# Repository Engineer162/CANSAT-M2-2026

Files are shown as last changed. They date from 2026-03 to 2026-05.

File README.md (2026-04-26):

# CANSAT-M2-2026 "Rod From God MK1"

This repository contains all the sources for a highly advanced CANSAT based on an STM32 MCU and featuring a rechargeable lithium polymer battery.

Core hardware fields:

| Component | Model | Manufacturer |
| --- | --- | --- |
| STM32 MCU (core) | STM32H7S3L8H6 | STMicroelectronics |

Power system:

| Component | Model | Manufacturer |
| --- | --- | --- |
| STM32 MCU (power)  | STM32L031G6U6 | STMicroelectronics |
| USB-C Connector | 12402012E212A | Amphenol |
| Battery Management | BQ25895RTWT | Texas Instruments  |
| PD Negotiation | TPS25730DREFR | Texas Instruments  |
| Battery | 1260110 (10000mAh LiPo) | TBD |

Additionally, it features numerous different sensors for logging, as listed below:

| Sensor | Model | Manufacturer |
| --- | --- | --- |
| IMU | ICM-42688-PC | Tokmas |
| Barometer | BMP581 | BOSCH |
| Magnetometer | MMC5983MA | MEMSIC |
| Temperature (outside) | TMP121AIDBVR | Texas Instruments  |
| Temperature (inside)  | TMP121AIDBVR | Texas Instruments  |
| Ground distance (ToF) | VL53L1CXV0FY/1 | STMicroelectronics |

And debugging/programming is done via a TAG-CONNECT TC2050-IDC "Plug-Of-Nails™" connector.

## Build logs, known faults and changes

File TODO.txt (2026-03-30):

TODO:

Check sensor INT pins to see if they are active_low or active_high.
Check sensor CS pins to see if they are active_low or active_high.
Check if the above pins need to be assigned as pin context to Application or otherwise.

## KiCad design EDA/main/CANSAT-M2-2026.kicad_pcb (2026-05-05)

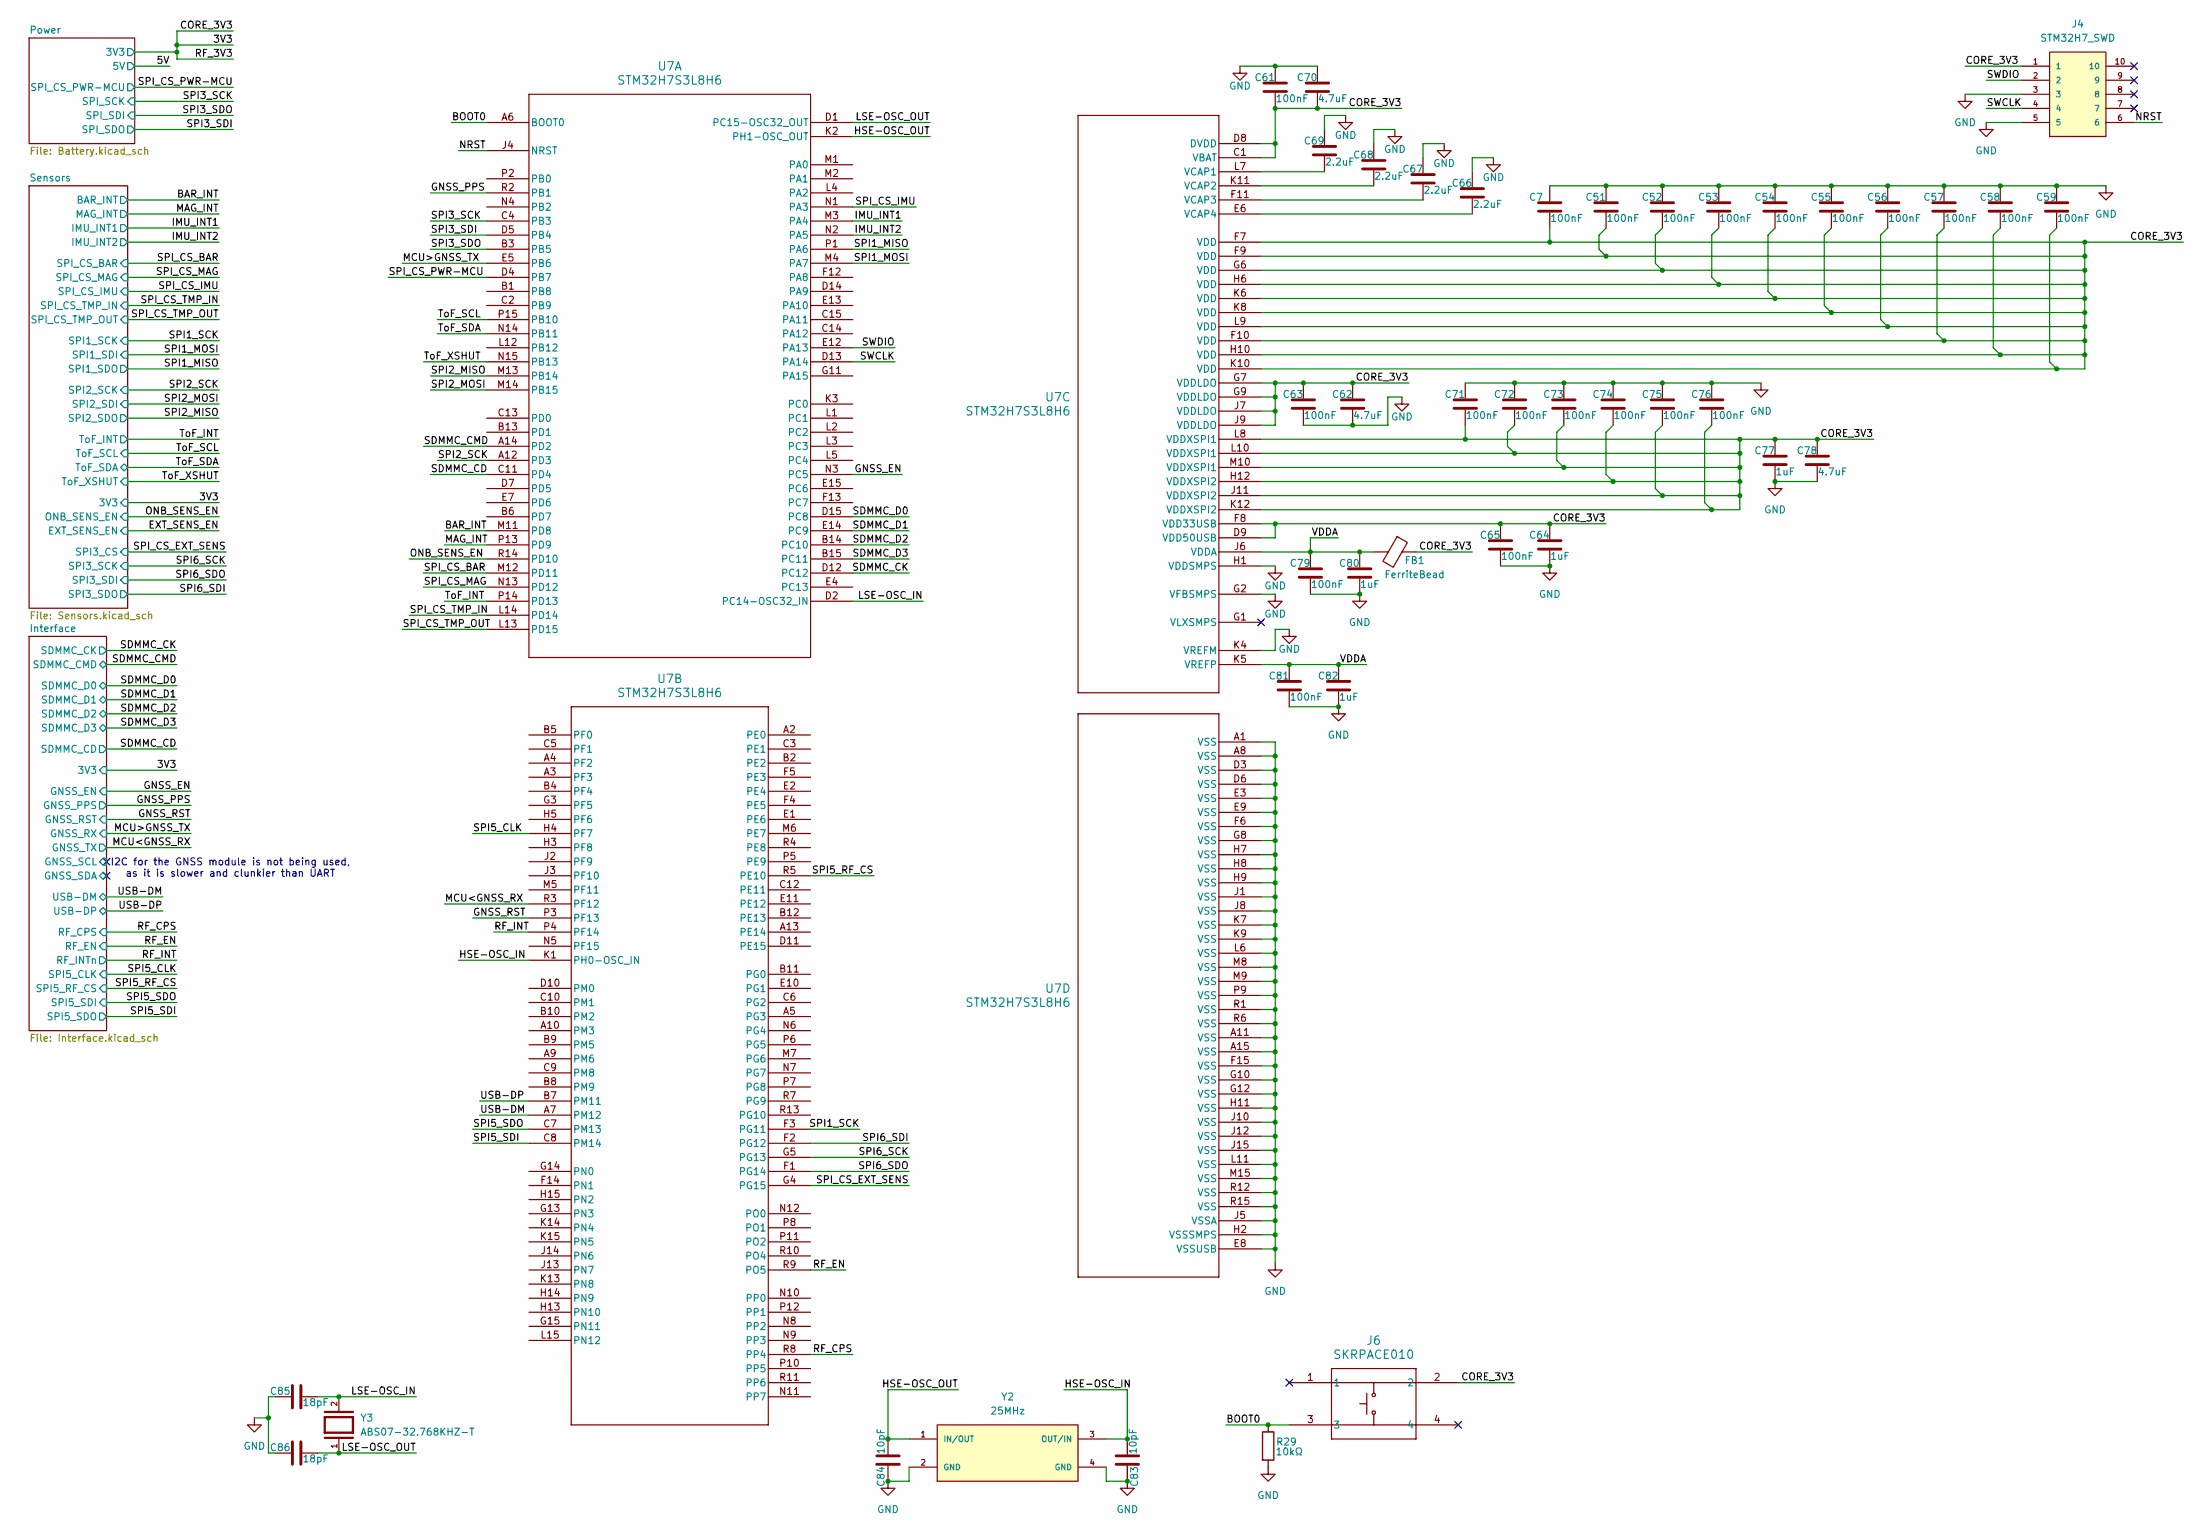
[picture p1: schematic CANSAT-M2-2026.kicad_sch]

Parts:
C7, C51, C52, C53, C54, C55, C56, C57, C58, C59, C61, C63, C65, C71, C72, C73, C74, C75, C76, C79, C81: 100nF; C_0402_1005Metric; Manufacturer Part CL05B104KP5NNNC
C62, C70, C78: 4.7uF; C_0603_1608Metric; Manufacturer Part CL10A475KP8NNNC
C64, C77, C80, C82: 1uF; C_0603_1608Metric; Manufacturer Part CL10B105MO8NNWC
C66, C67, C68, C69: 2.2uF; C_0603_1608Metric; Manufacturer Part CL10A225KO8NNNC
C83, C84: 10pF; C_0402_1005Metric; Manufacturer Part CL05C100JB5NNNC
C85, C86: 18pF; C_0402_1005Metric; Manufacturer Part CL05C180JB5NNNC
FB1: FerriteBead; L_0603_1608Metric; Manufacturer Part MMZ1608D121CTAH0
J4: STM32H7_SWD; TAG-CONNECT_TC2050-IDC; PARTREV A; DigiKey_Part_Number TC2050-IDC-ND
J6: SKRPACE010; SW_SKRPACE010_AAL; Manufacturer Part SKRPACE010
R29: 10kΩ; R_0402_1005Metric; Manufacturer Part RC0402FR-0710KL
U7: STM32H7S3L8H6; TFBGA225_13X13_STM; Manufacturer Part STM32H7S3L8H6H
Y2: 25MHz; XTAL_ECS-160-9-37-CKM-TR; PARTREV 2017
Y3: ABS07-32.768KHZ-T; XTAL_ABS07-32.768KHZ-T; PARTREV 08.19.15; DigiKey_Part_Number 535-9542-1-ND

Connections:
/3V3: C7.2, C51.2, C52.2, C53.2, C54.2, C55.2, C56.2, C57.2, C58.2, C59.2, C61.2, C62.1, C63.1, C64.1, C65.1, C70.2, C71.2, C72.2, C73.2, C74.2, C75.2, C76.2, C77.1, C78.1, FB1.1, J4.1, J6.2, U7.C1 (VBAT), U7.D8 (DVDD), U7.D9 (VDD50USB), U7.F7 (VDD), U7.F8 (VDD33USB), U7.F9 (VDD), U7.F10 (VDD), U7.G6 (VDD), U7.G7 (VDDLDO), U7.G9 (VDDLDO), U7.H6 (VDD), U7.H10 (VDD), U7.H12 (VDDXSPI2), U7.J7 (VDDLDO), U7.J9 (VDDLDO), U7.J11 (VDDXSPI2), U7.K6 (VDD), U7.K8 (VDD), U7.K10 (VDD), U7.K12 (VDDXSPI2), U7.L8 (VDDXSPI1), U7.L9 (VDD), U7.L10 (VDDXSPI1), U7.M10 (VDDXSPI1); also elsewhere on the board
/BAR_INT: U7.M11 (PD8); also elsewhere on the board
/BOOT0: J6.3, R29.1, U7.A6 (BOOT0)
/GNSS_EN: U7.N3 (PC5); also elsewhere on the board
/GNSS_PPS: U7.R2 (PB1); also elsewhere on the board
/GNSS_RST: U7.P3 (PF13); also elsewhere on the board
/HSE-OSC_IN: C83.2, U7.K1 (PH0-OSC_IN), Y2.3 (OUT/IN)
/HSE-OSC_OUT: C84.2, U7.K2 (PH1-OSC_OUT), Y2.1 (IN/OUT)
/IMU_INT1: U7.M3 (PA4); also elsewhere on the board
/IMU_INT2: U7.N2 (PA5); also elsewhere on the board
/LSE-OSC_IN: C85.2, U7.D2 (PC14-OSC32_IN), Y3.2
/LSE-OSC_OUT: C86.2, U7.D1 (PC15-OSC32_OUT), Y3.1
/MAG_INT: U7.P13 (PD9); also elsewhere on the board
/MCU<GNSS_RX: U7.R3 (PF12); also elsewhere on the board
/MCU>GNSS_TX: U7.E5 (PB6); also elsewhere on the board
/NRST: J4.6, U7.J4 (NRST)
/ONB_SENS_EN: U7.R14 (PD10); also elsewhere on the board
/RF_CPS: U7.R8 (PP4); also elsewhere on the board
/RF_EN: U7.R9 (PO5); also elsewhere on the board
/RF_INT: U7.P4 (PF14); also elsewhere on the board
/SDMMC_CD: U7.C11 (PD4); also elsewhere on the board
/SDMMC_CK: U7.D12 (PC12); also elsewhere on the board
/SDMMC_CMD: U7.A14 (PD2); also elsewhere on the board
/SDMMC_D0: U7.D15 (PC8); also elsewhere on the board
/SDMMC_D1: U7.E14 (PC9); also elsewhere on the board
/SDMMC_D2: U7.B14 (PC10); also elsewhere on the board
/SDMMC_D3: U7.B15 (PC11); also elsewhere on the board
/SPI1_MISO: U7.P1 (PA6); also elsewhere on the board
/SPI1_MOSI: U7.M4 (PA7); also elsewhere on the board
/SPI1_SCK: U7.F3 (PG11); also elsewhere on the board
/SPI2_MISO: U7.M13 (PB14); also elsewhere on the board
/SPI2_MOSI: U7.M14 (PB15); also elsewhere on the board
/SPI2_SCK: U7.A12 (PD3); also elsewhere on the board
/SPI3_SCK: U7.C4 (PB3); also elsewhere on the board
/SPI3_SDI: U7.D5 (PB4); also elsewhere on the board
/SPI3_SDO: U7.B3 (PB5); also elsewhere on the board
/SPI5_CLK: U7.H4 (PF7); also elsewhere on the board
/SPI5_RF_CS: U7.R5 (PE10); also elsewhere on the board
/SPI5_SDI: U7.C8 (PM14); also elsewhere on the board
/SPI5_SDO: U7.C7 (PM13); also elsewhere on the board
/SPI6_SCK: U7.G5 (PG13); also elsewhere on the board
/SPI6_SDI: U7.F2 (PG12); also elsewhere on the board
/SPI6_SDO: U7.F1 (PG14); also elsewhere on the board
/SPI_CS_BAR: U7.M12 (PD11); also elsewhere on the board
/SPI_CS_EXT_SENS: U7.G4 (PG15); also elsewhere on the board
/SPI_CS_IMU: U7.N1 (PA3); also elsewhere on the board
/SPI_CS_MAG: U7.N13 (PD12); also elsewhere on the board
/SPI_CS_PWR-MCU: U7.D4 (PB7); also elsewhere on the board
/SPI_CS_TMP_IN: U7.L14 (PD14); also elsewhere on the board
/SPI_CS_TMP_OUT: U7.L13 (PD15); also elsewhere on the board
/SWCLK: J4.4, U7.D13 (PA14)
/SWDIO: J4.2, U7.E12 (PA13)
/ToF_INT: U7.P14 (PD13); also elsewhere on the board
/ToF_SCL: U7.P15 (PB10); also elsewhere on the board
/ToF_SDA: U7.N14 (PB11); also elsewhere on the board
/ToF_XSHUT: U7.N15 (PB13); also elsewhere on the board
/USB-DM: U7.A7 (PM12); also elsewhere on the board
/USB-DP: U7.B7 (PM11); also elsewhere on the board
/VDDA: C79.1, C80.1, C81.1, C82.1, FB1.2, U7.J6 (VDDA), U7.K5 (VREFP)
GND: C7.1, C51.1, C52.1, C53.1, C54.1, C55.1, C56.1, C57.1, C58.1, C59.1, C61.1, C62.2, C63.2, C64.2, C65.2, C66.1, C67.1, C68.1, C69.1, C70.1, C71.1, C72.1, C73.1, C74.1, C75.1, C76.1, C77.2, C78.2, C79.2, C80.2, C81.2, C82.2, C83.1, C84.1, C85.1, C86.1, J4.3, J4.5, R29.2, U7.A1 (VSS), U7.A8 (VSS), U7.A11 (VSS), U7.A15 (VSS), U7.D3 (VSS), U7.D6 (VSS), U7.E3 (VSS), U7.E8 (VSSUSB), U7.E9 (VSS), U7.F6 (VSS), U7.F15 (VSS), U7.G2 (VFBSMPS), U7.G8 (VSS), U7.G10 (VSS), U7.G12 (VSS), U7.H1 (VDDSMPS), U7.H2 (VSSSMPS), U7.H7 (VSS), U7.H8 (VSS), U7.H9 (VSS), U7.H11 (VSS), U7.J1 (VSS), U7.J5 (VSSA), U7.J8 (VSS), U7.J10 (VSS), U7.J12 (VSS), U7.J15 (VSS), U7.K4 (VREFM), U7.K7 (VSS), U7.K9 (VSS), U7.L6 (VSS), U7.L11 (VSS), U7.M8 (VSS), U7.M9 (VSS), U7.M15 (VSS), U7.P9 (VSS), U7.R1 (VSS), U7.R6 (VSS), U7.R12 (VSS), U7.R15 (VSS), Y2.2 (GND), Y2.4 (GND); also elsewhere on the board
unnamed: C69.2, U7.L7 (VCAP1)
unnamed: C68.2, U7.K11 (VCAP2)
unnamed: C67.2, U7.F11 (VCAP3)
unnamed: C66.2, U7.E6 (VCAP4)

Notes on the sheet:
I2C for the GNSS module is not being used, as it is slower and clunkier than UART

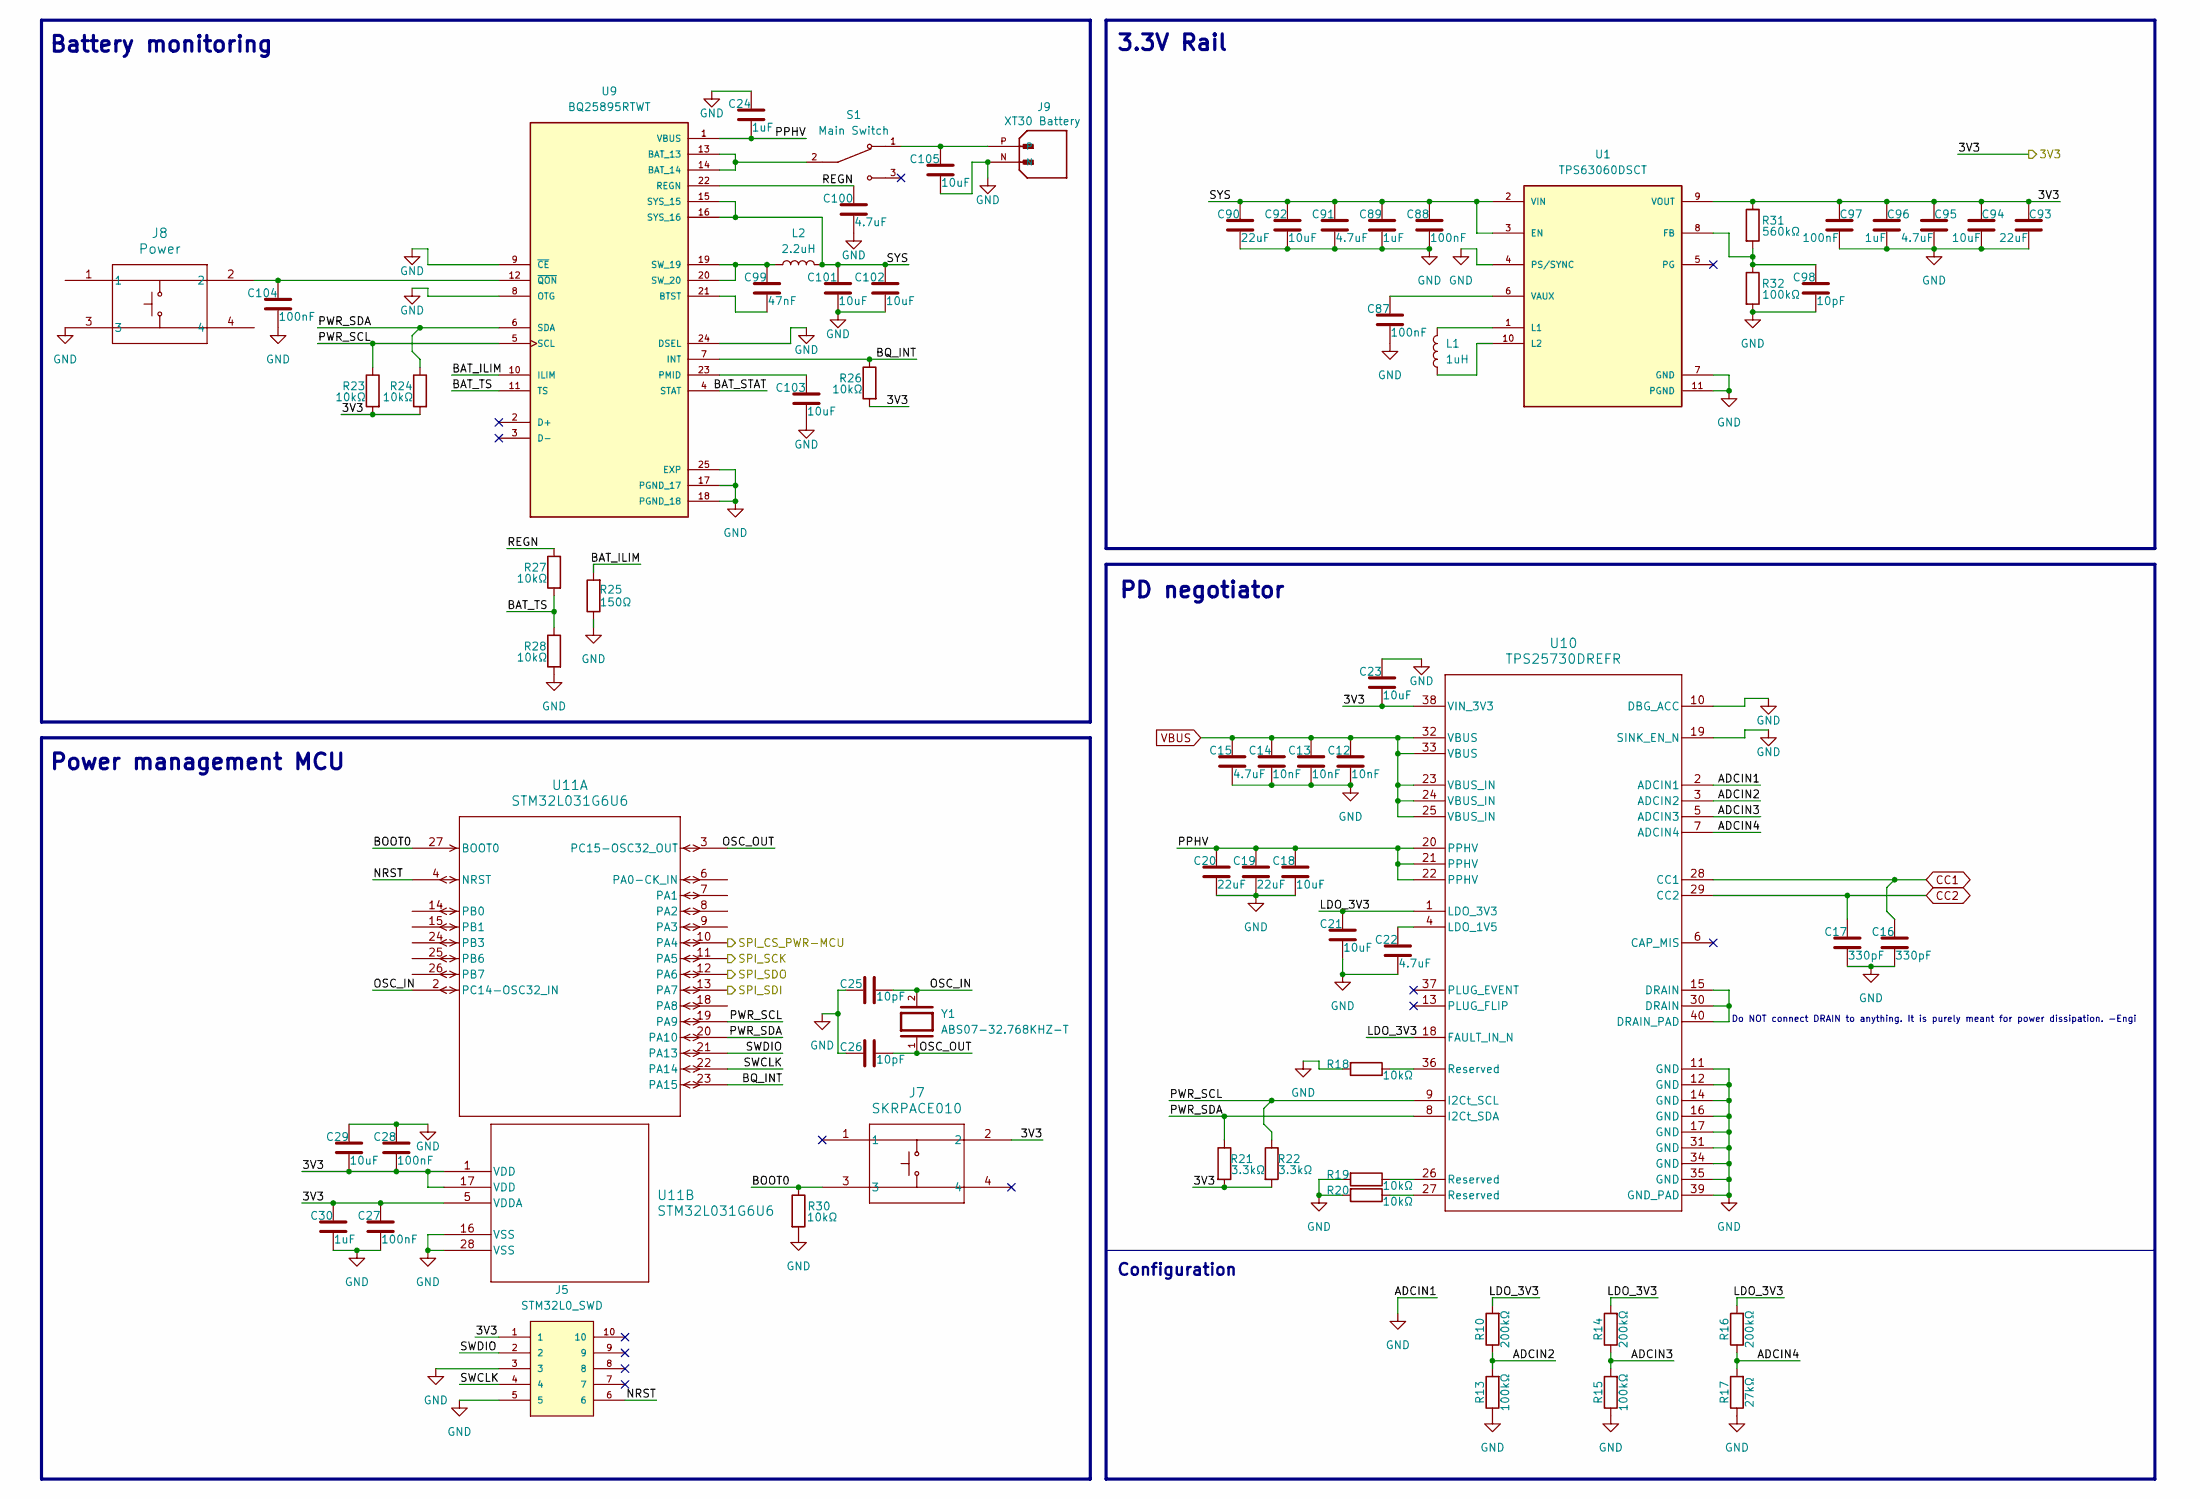
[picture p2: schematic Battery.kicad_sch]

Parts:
C12, C13, C14: 10nF; C_0402_1005Metric; Manufacturer Part CL05B103KB5NNNC
C15, C22, C91, C95, C100: 4.7uF; C_0603_1608Metric; Manufacturer Part CL10A475KP8NNNC
C16, C17: 330pF; C_0402_1005Metric; Manufacturer Part CL05C331JB5NNNC
C18, C21, C23, C29, C92, C94, C101, C102, C103, C105: 10uF; C_0603_1608Metric; Manufacturer Part CL10X106MO8NRNC
C19, C20, C90, C93: 22uF; C_0603_1608Metric; Manufacturer Part CL10A226MP8NUNE
C24, C30, C89, C96: 1uF; C_0603_1608Metric; Manufacturer Part CL10B105MO8NNWC
C25, C26, C98: 10pF; C_0402_1005Metric; Manufacturer Part CL05C100JB5NNNC
C27, C28, C87, C88, C97, C104: 100nF; C_0402_1005Metric; Manufacturer Part CL05B104KP5NNNC
C99: 47nF; C_0402_1005Metric; Manufacturer Part CL05B473KB5VPNC
J5: STM32L0_SWD; TAG-CONNECT_TC2050-IDC; PARTREV A; DigiKey_Part_Number TC2050-IDC-ND
J7: SKRPACE010; SW_SKRPACE010_AAL; Manufacturer Part SKRPACE010
J8: Power; SW_SKRPACE010_AAL; Manufacturer Part SKRPACE010
J9: XT30 Battery; AMASS_XT30PW-M; PARTREV 1.2
L1: 1uH; L_1008_2520Metric; Manufacturer Part 74438324010
L2: 2.2uH; L_Wuerth_MAPI-4020; Manufacturer Part 74438356022
R10, R14, R16: 200kΩ; R_0603_1608Metric; Manufacturer Part RC0603JR-07200KL
R13, R15: 100kΩ; R_0603_1608Metric; Manufacturer Part RC0603FR-07100KL
R17: 27kΩ; R_0603_1608Metric; Manufacturer Part RC0603FR-1027KL
R18, R19, R20, R23, R24, R26, R27, R28, R30: 10kΩ; R_0402_1005Metric; Manufacturer Part RC0402FR-0710KL
R21, R22: 3.3kΩ; R_0402_1005Metric; Manufacturer Part RC0402FR-073K3L
R25: 150Ω; R_0603_1608Metric; Manufacturer Part RC0603FR-07150RL
R31: 560kΩ; R_0402_1005Metric; Manufacturer Part RC0402FR-13560KL
R32: 100kΩ; R_0402_1005Metric; Manufacturer Part RC0402FR-07100KL
S1: Main Switch; SW_500SSP1S1M6QEA; PARTREV D
U1: TPS63060DSCT; CONV_TPS63060DSCT; PARTREV B
U9: BQ25895RTWT; QFN50P400X400X80-25N; PARTREV B
U10: TPS25730DREFR; REF0038A-MFG; Manufacturer Part TPS25730DREFR
U11: STM32L031G6U6; UFQFPN28-4x4mm; Manufacturer Part STM32L031G6U6
Y1: ABS07-32.768KHZ-T; XTAL_ABS07-32.768KHZ-T; PARTREV 08.19.15; DigiKey_Part_Number 535-9542-1-ND

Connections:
/3V3: C23.2, C27.1, C28.2, C29.2, C30.1, C93.1, C94.1, C95.1, C96.1, C97.1, J5.1, J7.2, R21.2, R22.2, R23.2, R24.2, R26.2, R31.1, U1.9 (VOUT), U10.38 (VIN_3V3), U11.1 (VDD), U11.5 (VDDA), U11.17 (VDD); also elsewhere on the board
/Power/ADCIN2: R10.1, R13.2, U10.3 (ADCIN2)
/Power/ADCIN3: R14.1, R15.2, U10.5 (ADCIN3)
/Power/ADCIN4: R16.1, R17.2, U10.7 (ADCIN4)
/Power/BAT_ILIM: R25.2, U9.10 (ILIM)
/Power/BAT_STAT: U9.4 (STAT)
/Power/BAT_TS: R27.2, R28.1, U9.11 (TS)
/Power/BOOT0: J7.3, R30.1, U11.27 (BOOT0)
/Power/BQ_INT: R26.1, U9.7 (INT), U11.23 (PA15)
/Power/LDO_3V3: C21.1, R10.2, R14.2, R16.2, U10.1 (LDO_3V3), U10.18 (FAULT_IN_N)
/Power/NRST: J5.6, U11.4 (NRST)
/Power/OSC_IN: C25.2, U11.2 (PC14-OSC32_IN), Y1.2
/Power/OSC_OUT: C26.2, U11.3 (PC15-OSC32_OUT), Y1.1
/Power/PPHV: C18.1, C19.1, C20.1, C24.2, U9.1 (VBUS), U10.20 (PPHV), U10.21 (PPHV), U10.22 (PPHV)
/Power/PWR_SCL: R22.1, R23.1, U9.5 (SCL), U10.9 (I2Ct_SCL), U11.19 (PA9)
/Power/PWR_SDA: R21.1, R24.1, U9.6 (SDA), U10.8 (I2Ct_SDA), U11.20 (PA10)
/Power/REGN: C100.1, R27.1, U9.22 (REGN)
/Power/SWCLK: J5.4, U11.22 (PA14)
/Power/SWDIO: J5.2, U11.21 (PA13)
/Power/SYS: C88.1, C89.1, C90.1, C91.1, C92.1, C101.1, C102.1, L2.2, U1.2 (VIN), U1.3 (EN), U9.15 (SYS_15), U9.16 (SYS_16)
/SPI3_SCK: U11.11 (PA5); also elsewhere on the board
/SPI3_SDI: U11.12 (PA6); also elsewhere on the board
/SPI3_SDO: U11.13 (PA7); also elsewhere on the board
/SPI_CS_PWR-MCU: U11.10 (PA4); also elsewhere on the board
CC1: C16.1, U10.28 (CC1); also elsewhere on the board
CC2: C17.1, U10.29 (CC2); also elsewhere on the board
GND: C12.2, C13.2, C14.2, C15.2, C16.2, C17.2, C18.2, C19.2, C20.2, C21.2, C22.2, C23.1, C24.1, C25.1, C26.1, C27.2, C28.1, C29.1, C30.2, C87.2, C88.2, C89.2, C90.2, C91.2, C92.2, C93.2, C94.2, C95.2, C96.2, C97.2, C98.2, C100.2, C101.2, C102.2, C103.2, C104.2, C105.2, J5.3, J5.5, J8.3, J9.N, R13.1, R15.1, R17.1, R18.2, R19.2, R20.2, R25.1, R28.2, R30.2, R32.2, U1.4 (PS/SYNC), U1.7 (GND), U1.11 (PGND), U9.8 (OTG), U9.9 (~CE), U9.17 (PGND_17), U9.18 (PGND_18), U9.24 (DSEL), U9.25 (EXP), U10.2 (ADCIN1), U10.10 (DBG_ACC), U10.11 (GND), U10.12 (GND), U10.14 (GND), U10.16 (GND), U10.17 (GND), U10.19 (SINK_EN_N), U10.31 (GND), U10.34 (GND), U10.35 (GND), U10.39 (GND_PAD), U11.16 (VSS), U11.28 (VSS); also elsewhere on the board
unnamed: C105.1, J9.P, S1.1
unnamed: R18.1, U10.36 (Reserved)
unnamed: R19.1, U10.26 (Reserved)
unnamed: R20.1, U10.27 (Reserved)
unnamed: C98.1, R31.2, R32.1, U1.8 (FB)
unnamed: L1.2, U1.1 (L1)
unnamed: L1.1, U1.10 (L2)
unnamed: C87.1, U1.6 (VAUX)
unnamed: S1.2, U9.13 (BAT_13), U9.14 (BAT_14)
unnamed: C99.2, U9.21 (BTST)
unnamed: C103.1, U9.23 (PMID)
unnamed: C99.1, L2.1, U9.19 (SW_19), U9.20 (SW_20)
unnamed: C104.1, J8.2, U9.12 (~QON)
unnamed: U10.15 (DRAIN), U10.30 (DRAIN), U10.40 (DRAIN_PAD)
unnamed: C22.1, U10.4 (LDO_1V5)
VBUS: C12.1, C13.1, C14.1, C15.1, U10.23 (VBUS_IN), U10.24 (VBUS_IN), U10.25 (VBUS_IN), U10.32 (VBUS), U10.33 (VBUS); also elsewhere on the board

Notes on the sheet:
Power management MCU
Battery monitoring
3.3V Rail
Configuration
Do NOT connect DRAIN to anything. It is purely meant for power dissipation. -Engi
PD negotiator

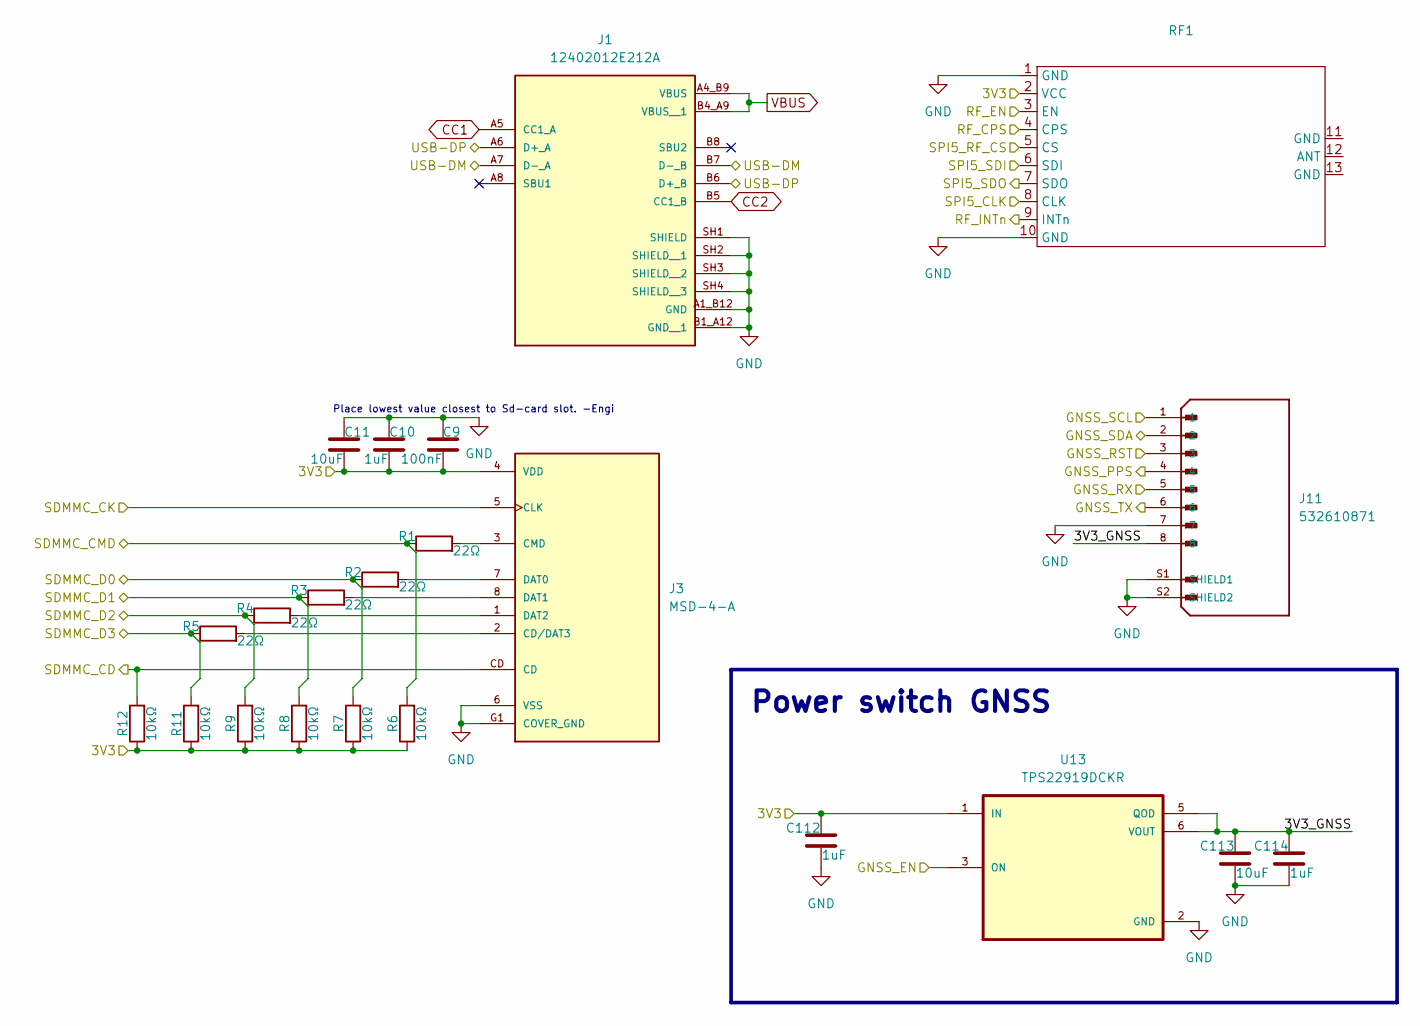
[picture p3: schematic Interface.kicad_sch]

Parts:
C9: 100nF; C_0402_1005Metric; Manufacturer Part CL05B104KP5NNNC
C10, C112, C114: 1uF; C_0603_1608Metric; Manufacturer Part CL10B105MO8NNWC
C11, C113: 10uF; C_0603_1608Metric; Manufacturer Part CL10X106MO8NRNC
J1: 12402012E212A; AMPHENOL_USB-C_12402012E212A; PARTREV 4
J3: MSD-4-A; CUI_MSD-4-A; PARTREV 1.0; DigiKey_Part_Number 2223-MSD-4-ACT-ND
J11: 532610871; MOLEX_532610871; PARTREV J
R1, R2, R3, R4, R5: 22Ω; R_0402_1005Metric; Manufacturer Part RC0402FR-0722RL
R6, R7, R8, R9, R11, R12: 10kΩ; R_0402_1005Metric; Manufacturer Part RC0402FR-0710KL
RF1: SI4463-MODULE
U13: TPS22919DCKR; SOT65P210X110-6N; Manufacturer Part TPS22919DCKR

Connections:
/3V3: C9.2, C10.2, C11.2, C112.1, J3.4 (VDD), R6.1, R7.1, R8.1, R9.1, R11.1, R12.1, RF1.2 (VCC), U13.1 (IN); also elsewhere on the board
/GNSS_EN: U13.3 (ON); also elsewhere on the board
/GNSS_PPS: J11.4; also elsewhere on the board
/GNSS_RST: J11.3; also elsewhere on the board
/Interface/3V3_GNSS: C113.1, C114.1, J11.8, U13.5 (QOD), U13.6 (VOUT)
/Interface/GNSS_SCL: J11.1
/Interface/GNSS_SDA: J11.2
/MCU<GNSS_RX: J11.6; also elsewhere on the board
/MCU>GNSS_TX: J11.5; also elsewhere on the board
/RF_CPS: RF1.4 (CPS); also elsewhere on the board
/RF_EN: RF1.3 (EN); also elsewhere on the board
/RF_INT: RF1.9 (INTn); also elsewhere on the board
/SDMMC_CD: J3.CD, R12.2; also elsewhere on the board
/SDMMC_CK: J3.5 (CLK); also elsewhere on the board
/SDMMC_CMD: R1.1, R6.2; also elsewhere on the board
/SDMMC_D0: R2.1, R7.2; also elsewhere on the board
/SDMMC_D1: R3.1, R8.2; also elsewhere on the board
/SDMMC_D2: R4.1, R9.2; also elsewhere on the board
/SDMMC_D3: R5.1, R11.2; also elsewhere on the board
/SPI5_CLK: RF1.8 (CLK); also elsewhere on the board
/SPI5_RF_CS: RF1.5 (CS); also elsewhere on the board
/SPI5_SDI: RF1.7 (SDO); also elsewhere on the board
/SPI5_SDO: RF1.6 (SDI); also elsewhere on the board
/USB-DM: J1.A7 (D-_A), J1.B7 (D-_B); also elsewhere on the board
/USB-DP: J1.A6 (D+_A), J1.B6 (D+_B); also elsewhere on the board
CC1: J1.A5 (CC1_A); also elsewhere on the board
CC2: J1.B5 (CC1_B); also elsewhere on the board
GND: C9.1, C10.1, C11.1, C112.2, C113.2, C114.2, J1.A1_B12 (GND), J1.B1_A12 (GND__1), J1.SH1 (SHIELD), J1.SH2 (SHIELD__1), J1.SH3 (SHIELD__2), J1.SH4 (SHIELD__3), J3.6 (VSS), J3.G1 (COVER_GND), J3.G2 (COVER_GND), J3.G3 (COVER_GND), J3.G4 (COVER_GND), J11.7, J11.S1 (SHIELD1), J11.S2 (SHIELD2), RF1.1 (GND), RF1.10 (GND), U13.2 (GND); also elsewhere on the board
unnamed: J3.2 (CD/DAT3), R5.2
unnamed: J3.3 (CMD), R1.2
unnamed: J3.7 (DAT0), R2.2
unnamed: J3.8 (DAT1), R3.2
unnamed: J3.1 (DAT2), R4.2
VBUS: J1.A4_B9 (VBUS), J1.B4_A9 (VBUS__1); also elsewhere on the board

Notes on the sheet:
Place lowest value closest to Sd-card slot. -Engi
Power switch GNSS

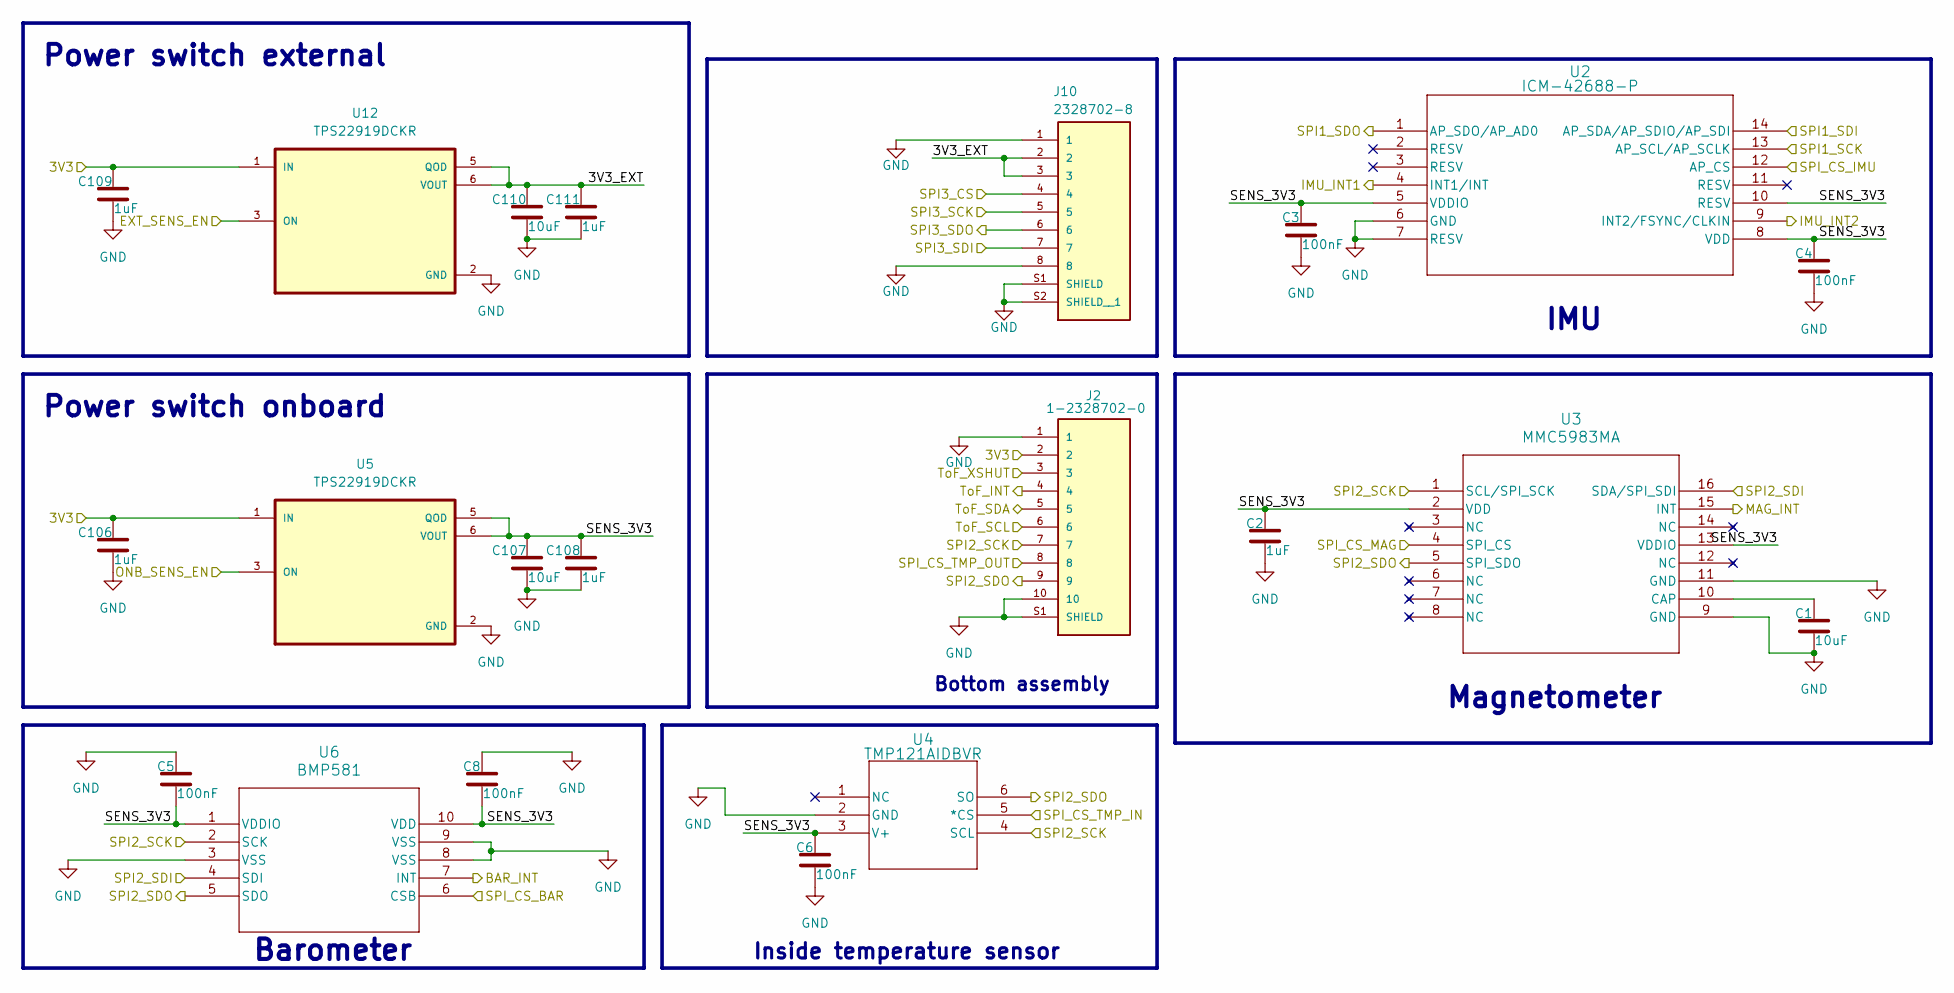
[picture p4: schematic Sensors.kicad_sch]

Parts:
C1, C107, C110: 10uF; C_0603_1608Metric; Manufacturer Part CL10X106MO8NRNC
C2, C106, C108, C109, C111: 1uF; C_0603_1608Metric; Manufacturer Part CL10B105MO8NNWC
C3, C4, C5, C6, C8: 100nF; C_0402_1005Metric; Manufacturer Part CL05B104KP5NNNC
J2: 1-2328702-0; TE_1-2328702-0; PARTREV 5; DigiKey_Part_Number A141390CT-ND
J10: 2328702-8; TE_2328702-8; PARTREV 5
U2: ICM-42688-P; LGA14_2P5X3X0P91_TDK; Manufacturer Part ICM-42688-P
U3: MMC5983MA; MMC5983MA_MEM; Manufacturer Part MMC5983MA
U4: TMP121AIDBVR; DBV6; Manufacturer Part TMP121AIDBVR
U5, U12: TPS22919DCKR; SOT65P210X110-6N; Manufacturer Part TPS22919DCKR
U6: BMP581; QFN10_BMP581_BOS; Manufacturer Part BMP581

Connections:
/3V3: C106.1, C109.1, J2.2, U5.1 (IN), U12.1 (IN); also elsewhere on the board
/BAR_INT: U6.7 (INT); also elsewhere on the board
/EXT_SENS_EN: U12.3 (ON)
/IMU_INT1: U2.4 (INT1/INT); also elsewhere on the board
/IMU_INT2: U2.9 (INT2/FSYNC/CLKIN); also elsewhere on the board
/MAG_INT: U3.15 (INT); also elsewhere on the board
/ONB_SENS_EN: U5.3 (ON); also elsewhere on the board
/SPI1_MISO: U2.1 (AP_SDO/AP_AD0); also elsewhere on the board
/SPI1_MOSI: U2.14 (AP_SDA/AP_SDIO/AP_SDI); also elsewhere on the board
/SPI1_SCK: U2.13 (AP_SCL/AP_SCLK); also elsewhere on the board
/SPI2_MISO: J2.9, U3.5 (SPI_SDO), U4.6 (SO), U6.5 (SDO); also elsewhere on the board
/SPI2_MOSI: U3.16 (SDA/SPI_SDI), U6.4 (SDI); also elsewhere on the board
/SPI2_SCK: J2.7, U3.1 (SCL/SPI_SCK), U4.4 (SCL), U6.2 (SCK); also elsewhere on the board
/SPI6_SCK: J10.5; also elsewhere on the board
/SPI6_SDI: J10.6; also elsewhere on the board
/SPI6_SDO: J10.7; also elsewhere on the board
/SPI_CS_BAR: U6.6 (CSB); also elsewhere on the board
/SPI_CS_EXT_SENS: J10.4; also elsewhere on the board
/SPI_CS_IMU: U2.12 (AP_CS); also elsewhere on the board
/SPI_CS_MAG: U3.4 (SPI_CS); also elsewhere on the board
/SPI_CS_TMP_IN: U4.5 (*CS); also elsewhere on the board
/SPI_CS_TMP_OUT: J2.8; also elsewhere on the board
/Sensors/3V3_EXT: C110.1, C111.1, J10.2, J10.3, U12.5 (QOD), U12.6 (VOUT)
/Sensors/SENS_3V3: C2.1, C3.1, C4.1, C5.2, C6.1, C8.2, C107.1, C108.1, U2.5 (VDDIO), U2.8 (VDD), U2.10 (RESV), U3.2 (VDD), U3.13 (VDDIO), U4.3 (V+), U5.5 (QOD), U5.6 (VOUT), U6.1 (VDDIO), U6.10 (VDD)
/ToF_INT: J2.4; also elsewhere on the board
/ToF_SCL: J2.6; also elsewhere on the board
/ToF_SDA: J2.5; also elsewhere on the board
/ToF_XSHUT: J2.3; also elsewhere on the board
GND: C1.2, C2.2, C3.2, C4.2, C5.1, C6.2, C8.1, C106.2, C107.2, C108.2, C109.2, C110.2, C111.2, J2.1, J2.10, J2.S1 (SHIELD), J2.S2 (SHIELD), J10.1, J10.8, J10.S1 (SHIELD), J10.S2 (SHIELD__1), U2.6 (GND), U2.7 (RESV), U3.9 (GND), U3.11 (GND), U4.2 (GND), U5.2 (GND), U6.3 (VSS), U6.8 (VSS), U6.9 (VSS), U12.2 (GND); also elsewhere on the board
unnamed: C1.1, U3.10 (CAP)

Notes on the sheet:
Power switch onboard
Barometer
Magnetometer
Bottom assembly
Inside temperature sensor
IMU
Power switch external

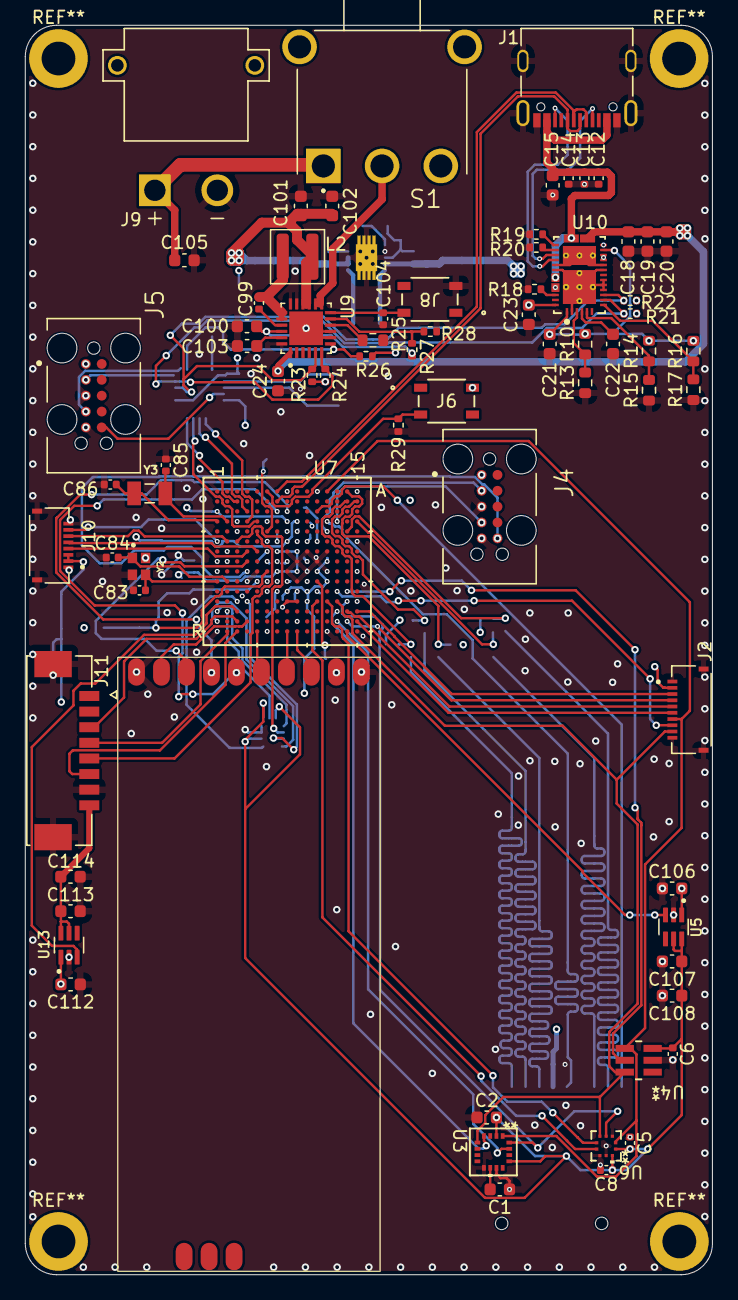
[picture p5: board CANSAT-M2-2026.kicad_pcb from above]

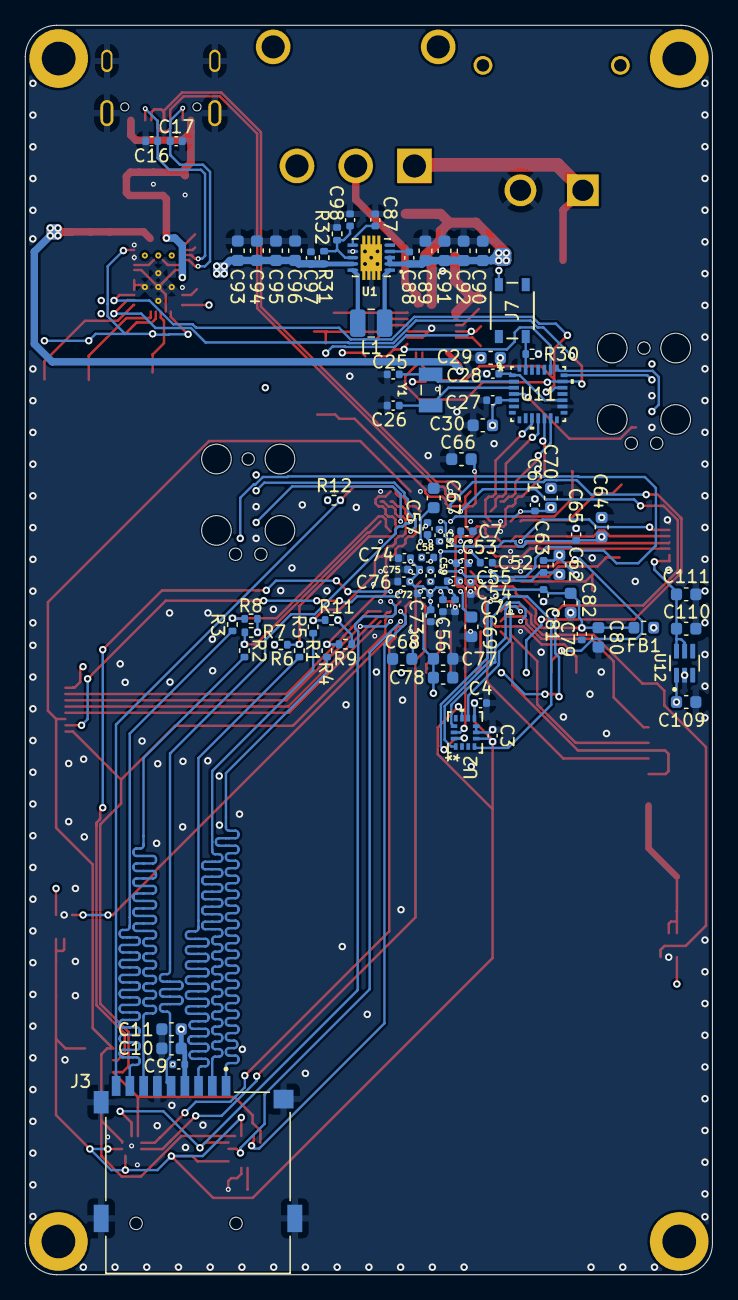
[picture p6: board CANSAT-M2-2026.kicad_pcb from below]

Board: 4 copper layers, 55.0 x 100.0 mm, 156 parts (83 on the bottom side), 109 nets.

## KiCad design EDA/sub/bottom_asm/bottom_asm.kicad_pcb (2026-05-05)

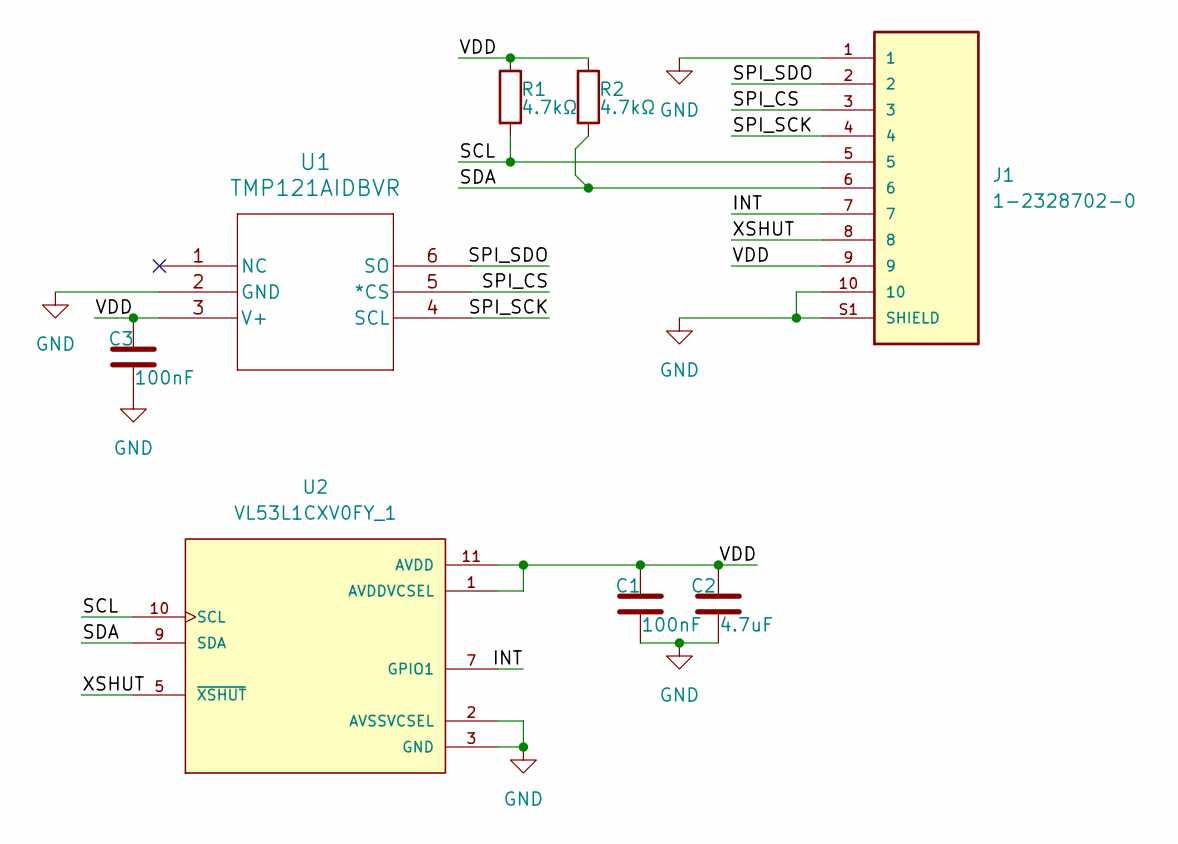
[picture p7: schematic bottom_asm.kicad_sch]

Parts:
C1, C3: 100nF; C_0402_1005Metric; Manufacturer Part CL05B104KP5NNNC
C2: 4.7uF; C_0603_1608Metric; Manufacturer Part CL10A475KP8NNNC
J1: 1-2328702-0; TE_1-2328702-0; PARTREV 5; DigiKey_Part_Number A141390CT-ND
R1, R2: 4.7kΩ; R_0402_1005Metric; Manufacturer Part RC0402JR-074K7L
U1: TMP121AIDBVR; DBV6; Manufacturer Part TMP121AIDBVR
U2: VL53L1CXV0FY_1; SENSOR_VL53L1CXV0FY_1; PARTREV 2

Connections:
/INT: J1.7, U2.7 (GPIO1)
/SCL: J1.5, R1.2, U2.10 (SCL)
/SDA: J1.6, R2.2, U2.9 (SDA)
/SPI_CS: J1.3, U1.5 (*CS)
/SPI_SCK: J1.4, U1.4 (SCL)
/SPI_SDO: J1.2, U1.6 (SO)
/VDD: C1.1, C2.1, C3.1, J1.9, R1.1, R2.1, U1.3 (V+), U2.1 (AVDDVCSEL), U2.11 (AVDD)
/XSHUT: J1.8, U2.5 (~XSHUT)
GND: C1.2, C2.2, C3.2, J1.1, J1.10, J1.S1 (SHIELD), J1.S2 (SHIELD), U1.2 (GND), U2.2 (AVSSVCSEL), U2.3 (GND), U2.4 (GND), U2.6 (GND), U2.12 (GND)

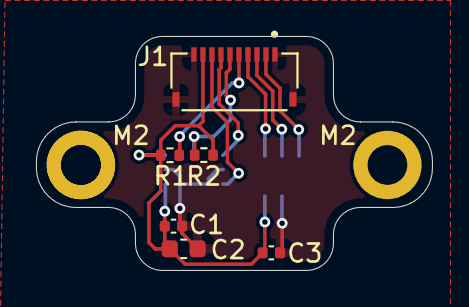
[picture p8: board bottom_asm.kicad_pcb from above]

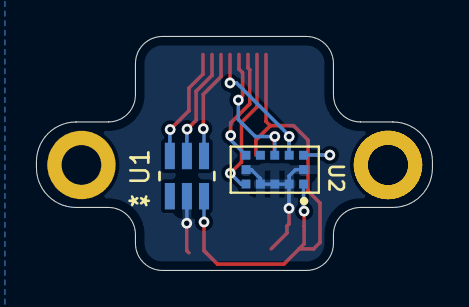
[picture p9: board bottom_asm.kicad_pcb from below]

Board: 2 copper layers, 22.0 x 13.0 mm, 10 parts (2 on the bottom side), 9 nets.

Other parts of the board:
M2, M2#2: MountingHole_2.2mm_M2_DIN965_Pad

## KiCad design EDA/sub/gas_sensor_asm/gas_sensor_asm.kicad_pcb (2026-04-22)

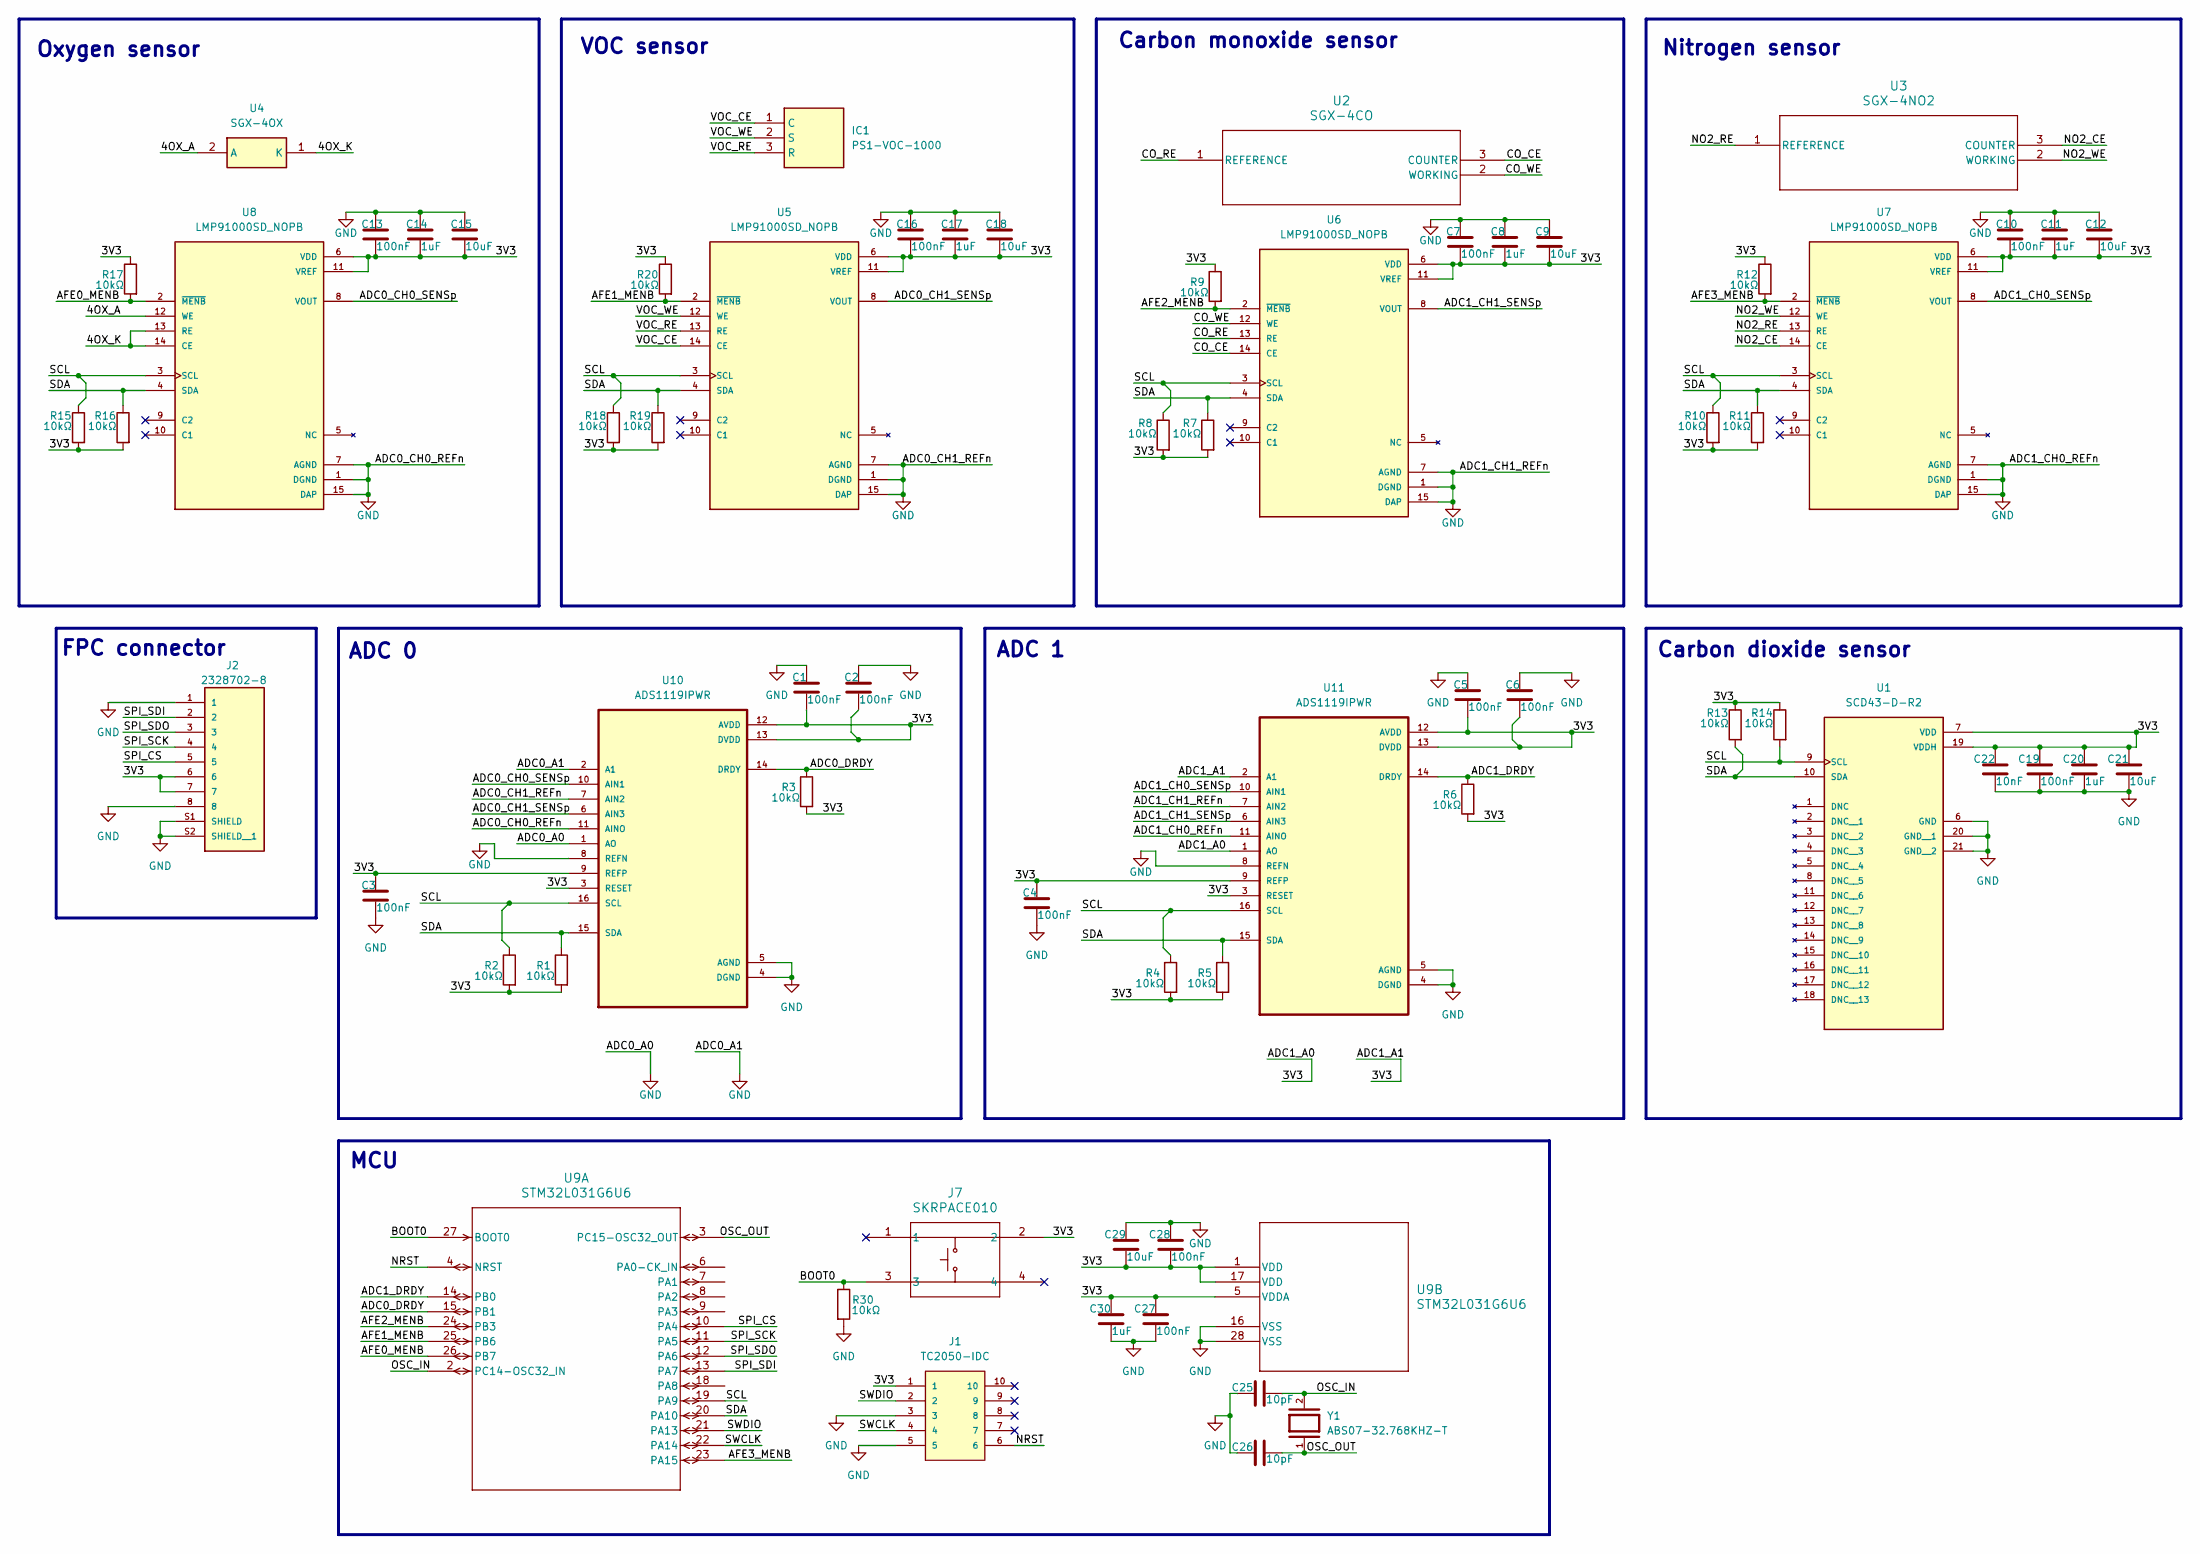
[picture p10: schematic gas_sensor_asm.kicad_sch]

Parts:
C1, C2, C3, C4, C5, C6, C7, C10, C13, C16, C19, C27, C28: 100nF; C_0402_1005Metric
C8, C11, C14, C17, C20, C30: 1uF; C_0603_1608Metric
C9, C12, C15, C18, C21, C29: 10uF; C_0603_1608Metric
C22: 10nF; C_0402_1005Metric
C25, C26: 10pF; C_0402_1005Metric
IC1: PS1-VOC-1000; PS1VOC1000; Manufacturer_Part_Number PS1-VOC-1000
J1: TC2050-IDC; TAG-CONNECT_TC2050-IDC; PARTREV A; DigiKey_Part_Number TC2050-IDC-ND
J2: 2328702-8; TE_2328702-8; PARTREV 5
J7: SKRPACE010; SW_SKRPACE010_AAL
R1, R2, R3, R4, R5, R6, R7, R8, R9, R10, R11, R12, R13, R14, R15, R16, R17, R18, R19, R20, R30: 10kΩ; R_0402_1005Metric
U1: SCD43-D-R2; XDCR_SCD43-D-R2; PARTREV 1.2
U2: SGX-4CO
U3: SGX-4NO2
U4: SGX-4OX; SGX4OX; Mouser Part Number 523-SGX-4OX
U5, U6, U7, U8: LMP91000SD_NOPB; SON50P400X400X80-15N; PARTREV I
U9: STM32L031G6U6; UFQFPN28-4x4mm
U10, U11: ADS1119IPWR; SOP65P640X120-16N
Y1: ABS07-32.768KHZ-T; XTAL_ABS07-32.768KHZ-T; PARTREV 08.19.15; DigiKey_Part_Number 535-9542-1-ND

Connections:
/3V3: C1.2, C2.2, C3.1, C4.1, C5.2, C6.2, C7.2, C8.2, C9.2, C10.2, C11.2, C12.2, C13.2, C14.2, C15.2, C16.2, C17.2, C18.2, C19.1, C20.1, C21.1, C22.1, C27.1, C28.2, C29.2, C30.1, J1.1, J2.6, J2.7, J7.2, R1.2, R2.2, R3.2, R4.2, R5.2, R6.2, R7.2, R8.2, R9.1, R10.2, R11.2, R12.1, R13.1, R14.1, R15.2, R16.2, R17.1, R18.2, R19.2, R20.1, U1.7 (VDD), U1.19 (VDDH), U5.6 (VDD), U5.11 (VREF), U6.6 (VDD), U6.11 (VREF), U7.6 (VDD), U7.11 (VREF), U8.6 (VDD), U8.11 (VREF), U9.1 (VDD), U9.5 (VDDA), U9.17 (VDD), U10.3 (RESET), U10.9 (REFP), U10.12 (AVDD), U10.13 (DVDD), U11.1 (AO), U11.2 (A1), U11.3 (RESET), U11.9 (REFP), U11.12 (AVDD), U11.13 (DVDD)
/4OX_A: U4.2 (A), U8.12 (WE)
/4OX_K: U4.1 (K), U8.13 (RE), U8.14 (CE)
/ADC0_CH0_SENSp: U8.8 (VOUT), U10.10 (AIN1)
/ADC0_CH1_SENSp: U5.8 (VOUT), U10.6 (AIN3)
/ADC0_DRDY: R3.1, U9.15 (PB1), U10.14 (DRDY)
/ADC1_CH0_SENSp: U7.8 (VOUT), U11.10 (AIN1)
/ADC1_CH1_SENSp: U6.8 (VOUT), U11.6 (AIN3)
/ADC1_DRDY: R6.1, U9.14 (PB0), U11.14 (DRDY)
/AFE0_MENB: R17.2, U8.2 (~MENB), U9.26 (PB7)
/AFE1_MENB: R20.2, U5.2 (~MENB), U9.25 (PB6)
/AFE2_MENB: R9.2, U6.2 (~MENB), U9.24 (PB3)
/AFE3_MENB: R12.2, U7.2 (~MENB), U9.23 (PA15)
/BOOT0: J7.3, R30.1, U9.27 (BOOT0)
/CO_CE: U2.3 (COUNTER), U6.14 (CE)
/CO_RE: U2.1 (REFERENCE), U6.13 (RE)
/CO_WE: U2.2 (WORKING), U6.12 (WE)
/NO2_CE: U3.3 (COUNTER), U7.14 (CE)
/NO2_RE: U3.1 (REFERENCE), U7.13 (RE)
/NO2_WE: U3.2 (WORKING), U7.12 (WE)
/NRST: J1.6, U9.4 (NRST)
/OSC_IN: C25.2, U9.2 (PC14-OSC32_IN), Y1.2
/OSC_OUT: C26.2, U9.3 (PC15-OSC32_OUT), Y1.1
/SCL: R2.1, R4.1, R8.1, R10.1, R14.2, R15.1, R18.1, U1.9 (SCL), U5.3 (SCL), U6.3 (SCL), U7.3 (SCL), U8.3 (SCL), U9.19 (PA9), U10.16 (SCL), U11.16 (SCL)
/SDA: R1.1, R5.1, R7.1, R11.1, R13.2, R16.1, R19.1, U1.10 (SDA), U5.4 (SDA), U6.4 (SDA), U7.4 (SDA), U8.4 (SDA), U9.20 (PA10), U10.15 (SDA), U11.15 (SDA)
/SPI_CS: J2.5, U9.10 (PA4)
/SPI_SCK: J2.4, U9.11 (PA5)
/SPI_SDI: J2.2, U9.13 (PA7)
/SPI_SDO: J2.3, U9.12 (PA6)
/SWCLK: J1.4, U9.22 (PA14)
/SWDIO: J1.2, U9.21 (PA13)
/VOC_CE: IC1.1 (C), U5.14 (CE)
/VOC_RE: IC1.3 (R), U5.13 (RE)
/VOC_WE: IC1.2 (S), U5.12 (WE)
GND: C1.1, C2.1, C3.2, C4.2, C5.1, C6.1, C7.1, C8.1, C9.1, C10.1, C11.1, C12.1, C13.1, C14.1, C15.1, C16.1, C17.1, C18.1, C19.2, C20.2, C21.2, C22.2, C25.1, C26.1, C27.2, C28.1, C29.1, C30.2, J1.3, J1.5, J2.1, J2.8, J2.S1 (SHIELD), J2.S2 (SHIELD__1), R30.2, U1.6 (GND), U1.20 (GND__1), U1.21 (GND__2), U5.1 (DGND), U5.7 (AGND), U5.15 (DAP), U6.1 (DGND), U6.7 (AGND), U6.15 (DAP), U7.1 (DGND), U7.7 (AGND), U7.15 (DAP), U8.1 (DGND), U8.7 (AGND), U8.15 (DAP), U9.16 (VSS), U9.28 (VSS), U10.1 (AO), U10.2 (A1), U10.4 (DGND), U10.5 (AGND), U10.7 (AIN2), U10.8 (REFN), U10.11 (AINO), U11.4 (DGND), U11.5 (AGND), U11.7 (AIN2), U11.8 (REFN), U11.11 (AINO)

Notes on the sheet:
Nitrogen sensor
Carbon monoxide sensor
ADC 0
MCU
VOC sensor
FPC connector
Carbon dioxide sensor
ADC 1
Oxygen sensor

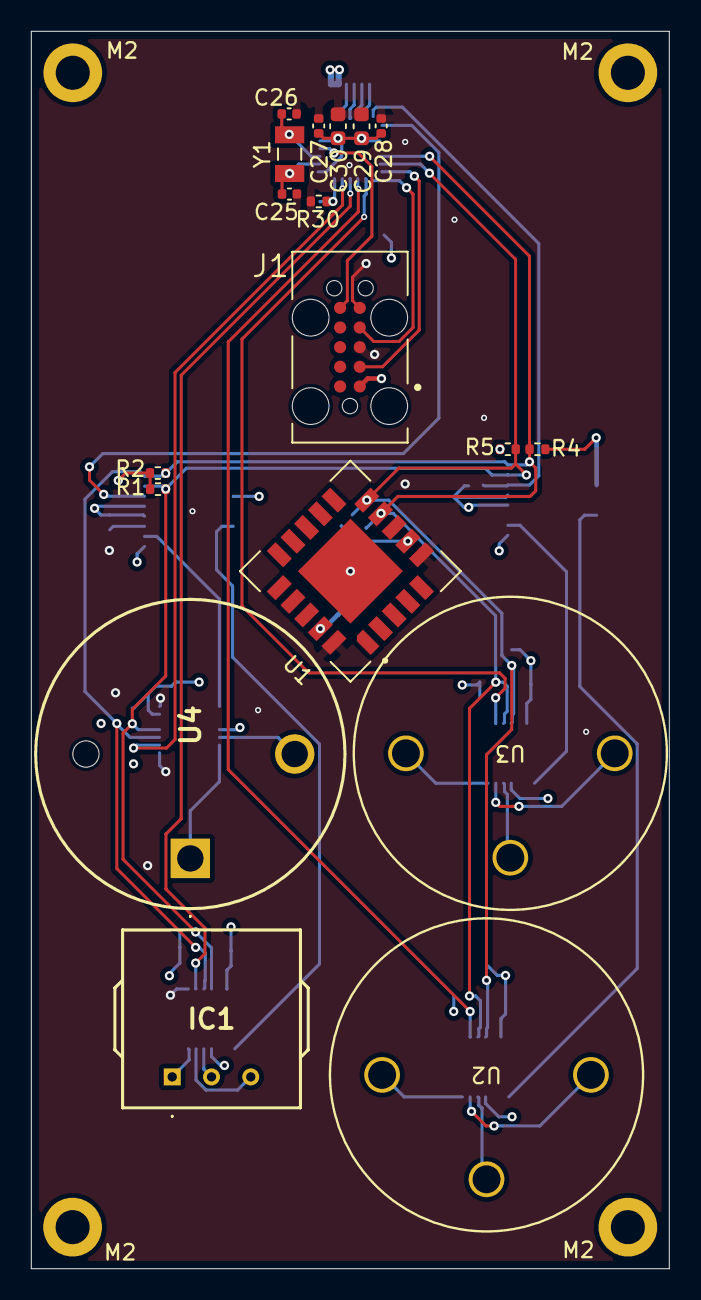
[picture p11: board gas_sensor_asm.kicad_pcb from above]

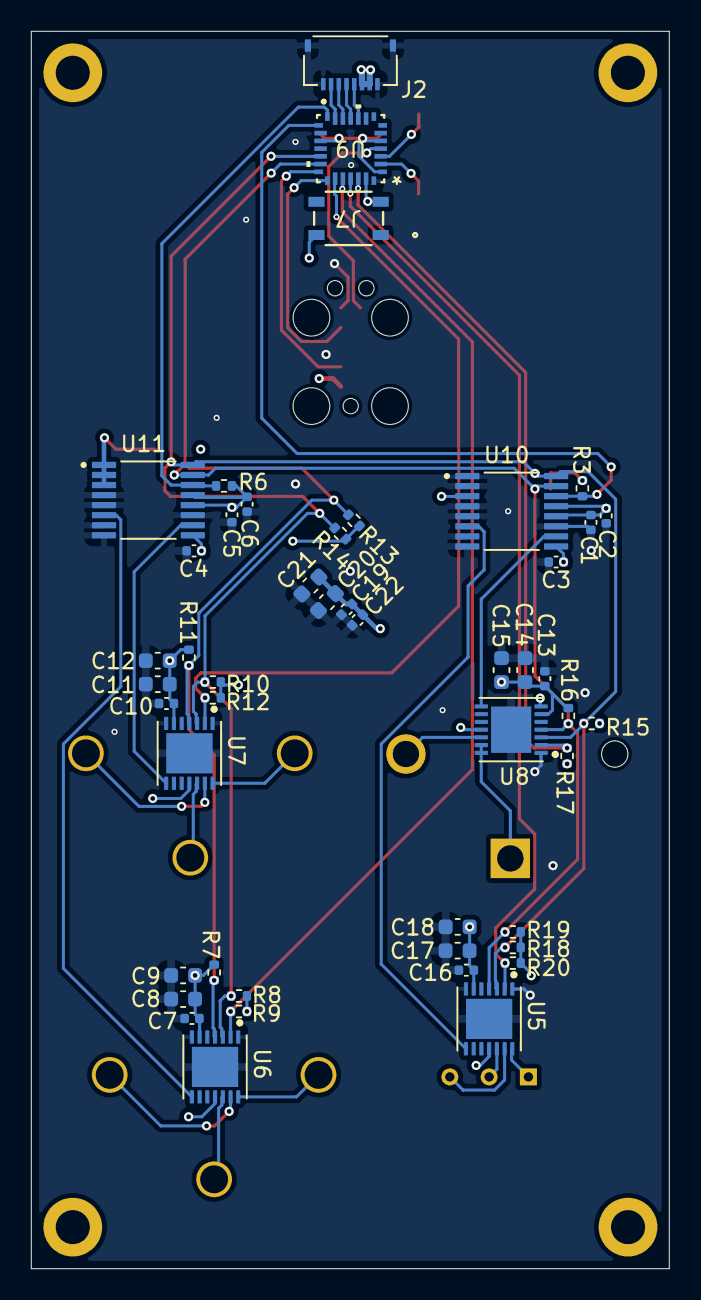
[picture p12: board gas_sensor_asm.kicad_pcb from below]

Board: 4 copper layers, 41.2 x 80.0 mm, 69 parts (47 on the bottom side), 35 nets.

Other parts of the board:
M2, M2#2, M2#3, M2#4: MountingHole_2.2mm_M2_DIN965_Pad

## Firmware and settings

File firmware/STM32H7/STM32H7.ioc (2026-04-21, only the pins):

Mcu.UserName=STM32H7S3L8Hx
PA10.Signal=FMC_D2_DA2
PA11.Signal=FMC_D1_DA1
PA12.Signal=FMC_D0_DA0
PA13(JTMS/SWDIO).Signal=DEBUG_JTMS-SWDIO
PA14(JTCK/SWCLK).Signal=DEBUG_JTCK-SWCLK
PA3.GPIO_Label=SPI_CS_IMU
PA3.Signal=GPIO_Output
PA4.GPIO_Label=IMU_INT1
PA4.Signal=GPXTI4
PA5.GPIO_Label=IMU_INT2
PA5.Signal=GPXTI5
PA6.Signal=SPI1_MISO
PA8.Signal=FMC_D4_DA4
PA9.Signal=FMC_D3_DA3
PB10.Signal=I2C2_SCL
PB11.Signal=I2C2_SDA
PB13.GPIO_Label=ToF_XSHUT
PB13.Signal=GPIO_Output
PB14.Signal=SPI2_MISO
PB15.Signal=SPI2_MOSI
PB3(JTDO/TRACESWO).Signal=SPI3_SCK
PB4(NJTRST).Signal=SPI3_MISO
PB5.Signal=SPI1_MOSI
PB7.GPIO_Label=SPI_CS_PWR-MCU
PB7.Signal=GPIO_Output
PC0.Signal=FMC_NBL1
PC1.Signal=FMC_A0
PC10.Signal=SDMMC1_D2
PC11.Signal=SDMMC1_D3
PC12.Signal=SDMMC1_CK
PC14-OSC32_IN(OSC32_IN).Signal=RCC_OSC32_IN
PC15-OSC32_OUT(OSC32_OUT).Signal=RCC_OSC32_OUT
PC2.Signal=FMC_A1
PC3.Signal=FMC_A2
PC4.Signal=FMC_A3
PC5.Signal=FMC_A5
PC8.Signal=SDMMC1_D0
PC9.Signal=SDMMC1_D1
PD0.Signal=FMC_A6
PD1.Signal=FMC_A7
PD11.GPIO_Label=SPI_CS_BAR
PD11.Signal=GPIO_Output
PD12.GPIO_Label=SPI_CS_MAG
PD12.Signal=GPIO_Output
PD13.GPIO_Label=ToF_INT
PD13.Signal=GPXTI13
PD14.GPIO_Label=SPI_CS_TMP_IN
PD14.Signal=GPIO_Output
PD15.GPIO_Label=SPI_CS_TMP_OUT
PD15.Signal=GPIO_Output
PD2.Signal=SDMMC1_CMD
PD3.Signal=SPI2_SCK
PD6.Signal=SPI3_MOSI
PD7.Signal=FMC_D8_DA8
PD8.GPIO_Label=BAR_INT
PD8.Signal=GPXTI8
PD9.GPIO_Label=MAG_INT
PD9.Signal=GPXTI9
PE0.Signal=FMC_D9_DA9
PE1.Signal=FMC_D10_DA10
PE10.Signal=FMC_A15_BA1
PE11.Signal=FMC_SDNWE
PE12.Signal=FMC_SDNRAS
PE13.Signal=FMC_SDNCAS
PE14.Signal=FMC_SDNE0
PE15.Signal=FMC_SDCKE0
PE2.Signal=FMC_D11_DA11
PE3.Signal=FMC_D12_DA12
PE4.Signal=FMC_D13_DA13
PE5.Signal=FMC_D14_DA14
PE6.Signal=FMC_D15_DA15
PE7.Signal=FMC_A4
PE9.Signal=FMC_A14_BA0
PF0.Signal=FMC_A8
PF1.Signal=FMC_A9
PF2.Signal=FMC_A10
PF3.Signal=FMC_A11
PG11.Signal=SPI1_SCK
PG12.Signal=SPI6_MISO
PG13.Signal=SPI6_SCK
PG14.Signal=SPI6_MOSI
PG15.GPIO_Label=SPI_CS_EXT_SENS
PG15.Signal=GPIO_Output
PH0-OSC_IN(PH0).Signal=RCC_OSC_IN
PH1-OSC_OUT(PH1).Signal=RCC_OSC_OUT

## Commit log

2026-02-06 Uploaded sensor schematic
2026-02-06 update README with project overview and sensors
    Added project description and sensor details to README.
2026-03-10 Changed barometer to BOSCH BMP581, and added outside and inside temperature sensors.
2026-03-25 Ported EDA from EasyEDA to KiCad
    [Battery.kicad_sch, CANSAT-M2-2026.kicad_sch, Interface.kicad_sch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]
2026-03-25 Changed STM32 MCU type, and added SDRAM. Micro-SD card slot has also been set up.
    [Interface.kicad_sch, MCU.kicad_sch, Sensors.kicad_sch]
2026-03-26 Added USB-C power negotiator and battery charger
2026-03-26 Choose USB-C connector to be used
2026-03-26 Changed PD IC from TPS25750DRJKR to TPS25730DREFR
    [Battery.kicad_sch, MCU.kicad_sch]
2026-03-27 added smoothing capacitors to PD IC
    [Battery.kicad_sch, Interface.kicad_sch]
2026-03-27 PD negotiator IC wired up in schematic
    [Battery.kicad_sch]
2026-03-28 Did some scheamtic restruscturing as well as hooked up SDRAM and Micro-SD to STM32 core. Additional low power STM32 has also been added to power control. Firmware .IOC files have also been added for 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
    [Battery.kicad_sch, CANSAT-M2-2026.kicad_sch, Interface.kicad_sch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]
2026-03-30 Project restructure, and added a bottom assembly PCB.
    [Battery.kicad_sch, CANSAT-M2-2026.kicad_sch, Interface.kicad_sch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]
2026-03-30 Assigned CS and INT from sensors, and added SWD to PWR-MCU and CORE-MCU
    [Battery.kicad_sch, CANSAT-M2-2026.kicad_sch, Interface.kicad_sch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]
2026-04-20 Uploaded work
    [Battery.kicad_sch, CANSAT-M2-2026.kicad_sch, Interface.kicad_sch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]
2026-04-20 Added gas sensor sub-board
    [gas_sensor_asm.kicad_pcb, gas_sensor_asm.kicad_sch]
2026-04-21 Finished gas sensor PCB, and added connector for it on main PCB
    [CANSAT-M2-2026.kicad_sch, Sensors.kicad_sch, gas_sensor_asm.kicad_sch]
2026-04-22 Added GNSS and SIM800L
    [Battery.kicad_sch, CANSAT-M2-2026.kicad_pcb, CANSAT-M2-2026.kicad_sch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]
2026-04-26 Worked on SDRAM
    [CANSAT-M2-2026.kicad_pcb]
2026-04-26 Made main branch not include SDRAM
    [CANSAT-M2-2026.kicad_sch, SDRAM.kicad_sch]
2026-05-05 PCB done
    [Battery.kicad_sch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]
